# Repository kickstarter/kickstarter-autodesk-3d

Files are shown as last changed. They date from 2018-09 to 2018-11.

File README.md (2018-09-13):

# Using the Autodesk x Kickstarter FDM 3D Printer Assessment
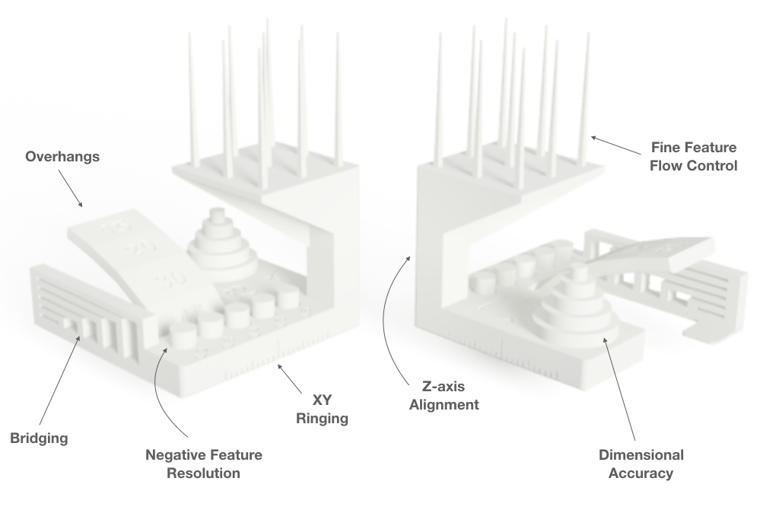
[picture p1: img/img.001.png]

## Background and Rationale
Autodesk and Kickstarter have developed a common standard that enables people to assess the performance of FDM 3D printers. (You can read more about why we undertook this initiative [here](https://www.kickstarter.com/blog/2221).) The features composing this geometry are largely based off the collaboration between Andreas Bastian and Make Magazine to develop Make Magazine’s early 3D printer shootout benchmarking protocol.

The geometry we’ve developed tests how well a printer’s hardware and software are calibrated to a given material by stressing the system to the point of failure.  The failures lead to the creation of witness features that can be used to assess the performance of the slicer, the extruder, and the motion system.  While this geometry and protocol can reveal many different types of problems in a system, fixing the exposed problems is out of scope for this basic assessment protocol.

It’s important to create dedicated test features and to calibrate those features to guarantee at least partial process failure: causing failure allows you to confirm that you’ve actually reached the limits of a process, and provides something discrete to measure and compare as relevant variables are changed.

Having discrete tests that each are calibrated to cause process failure, however, can become difficult to manage as the number of specialized tests grows, so having a consolidated geometry makes the process of testing a new 3D printer more manageable. We designed geometry to group non-interfering test features in the lower half of the print and places the riskier feature at the top of the print so that it doesn’t interfere with earlier test features.

## Contributing
We’re releasing with version 4 of this geometry and would like to work with the community of testers and creators to continue to refine and build upon both this test geometry and the test protocol, both for FDM and soon for SLA, SLS, and metal AM machines as well.  Please share comments, suggestions for improvements, and other ideas by opening an issue on this repo or submitting a pull request. And, be sure to tag photos of your prints with #FDMtest!

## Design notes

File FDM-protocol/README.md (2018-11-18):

## FDM Assessment Protocol

Download the [latest test geometry](./ksr_fdmtest_v4.stl) (units are mm) from the FDM-protocol folder and print the geometry using ESUN PLA+ Cool White filament, available in both [1.75mm](https://www.amazon.com/gp/product/B01EKEMFQS) and [2.85mm](https://www.amazon.com/dp/B01EKFV60S/) sizes using “standard” settings (i.e. all default settings).  It is very important to use the same material, as rheological and thermal properties of materials can vary dramatically between manufacturers, effectively invalidating any results obtained without controlling material properties.

What this geometry does test:

* Dimensional accuracy (backlash optional)
* Negative feature resolution
* Positive feature resolution/fine flow control
* Basic overhang capabilities
* Basic bridging capabilities
* XY ringing
* Z-axis alignment

What this geometry does not test:

* Warp/adhesion
* Overhang capabilities over a range of features (concave, convex, etc)
* Slicer handling of fine XY plane features (positive and negative space)
* Complex bridging situations
* Surface finish over a range of features
* Extrusion temperature optimization
* Support structure/geometry interaction

This geometry can be used both to characterize and compare different 3D printers and to tune parameters relevant to different features present in the geometry.

### 1. Dimensional Accuracy

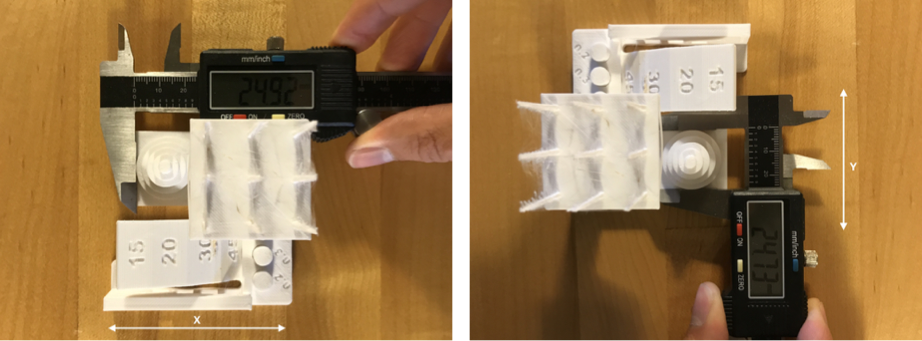
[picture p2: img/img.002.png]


*To assess dimensional accuracy, measure each tier of the dimensional accuracy stack and record the absolute different between the target and the measured dimensions in a table like so:*

**Target**|**Measured X**|**Measured Y**|**X Error**|**Y Error**
:-----:|:-----:|:-----:|:-----:|:-----:
25|24.82|24.69|0.18|0.31
20|19.93|19.75|0.07|0.25
15|14.99|14.82|0.01|0.18
10|10.01|9.85|0.01|0.15
5|4.84|4.84|0.16|0.16
Avg Err:|0.082|0.21| |
 **Average of avg. X and avg. Y error** | **0.146** | | |
Difference between avg. X and avg. Y error|0.128| | |

* Record a “1” if the magnitude of the overall average error is greater than 0.40mm.
* Record a “2” if the magnitude of the overall average error is between 0.31 and 0.40mm.
* Record a “3” if the magnitude of the overall average error is between 0.21 and 0.30mm.
* Record a “4” if the magnitude of the overall average error is 0.11 and 0.20mm.
* Record a “5” if the magnitude of the overall average error is between 0.0 and 0.10mm.

While it is not explicitly scored in this evaluation, this test also reveals the presence of backlash (or incorrectly calibrated motion systems) when the average X and average Y errors are compared.  A significant difference between the two values indicates a problem.  

### 2. Fine Flow Control

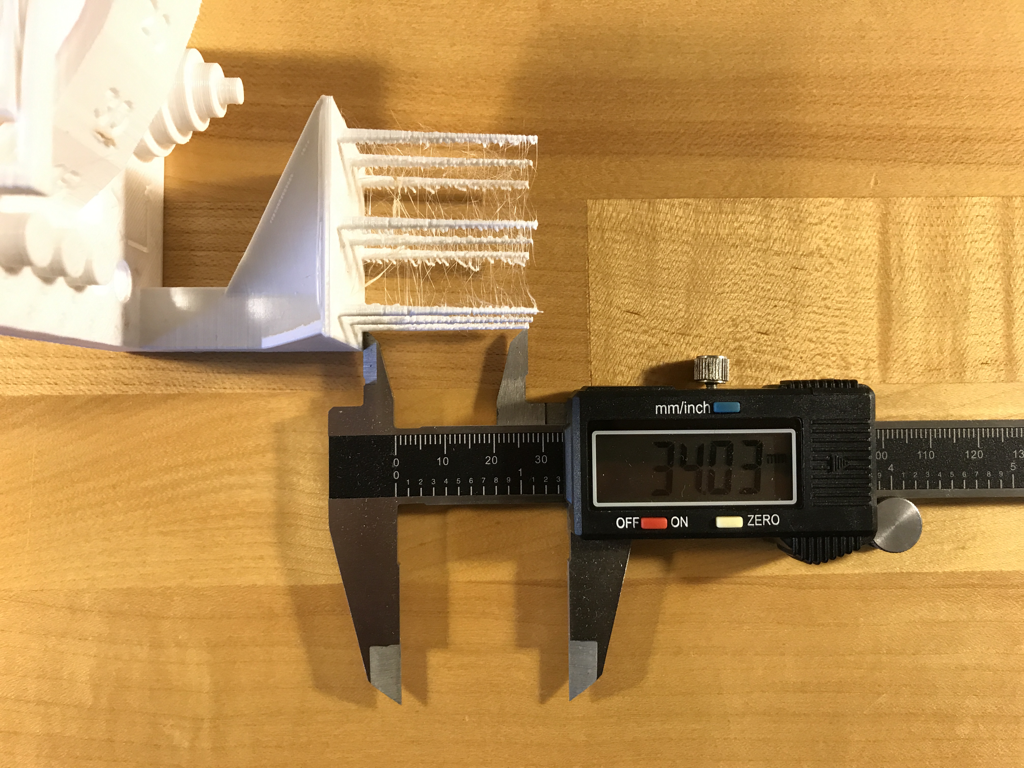
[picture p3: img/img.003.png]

*Using a pair of calipers, measure the height of the shortest spire on the top of the test print.  Visually inspect for threads of material connecting the spires.*

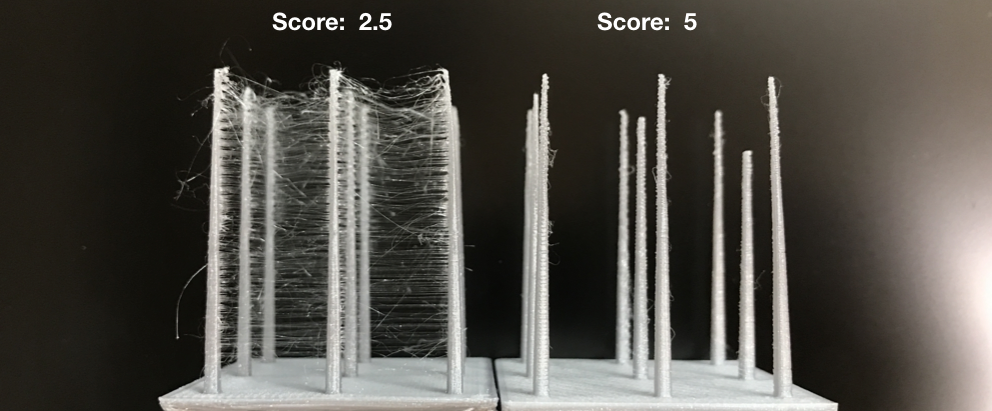
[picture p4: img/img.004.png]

*Measure the shortest spire.  This print would score 2.5.*

* If the spires are less than 30mm long, assign a 0.
* If the spires are greater than 30mm, but there is stringing between them, assign a 2.5.
* If the spires are greater than 30mm long and there is no stringing between them, assign a 5.  

### 3. Fine Negative Features

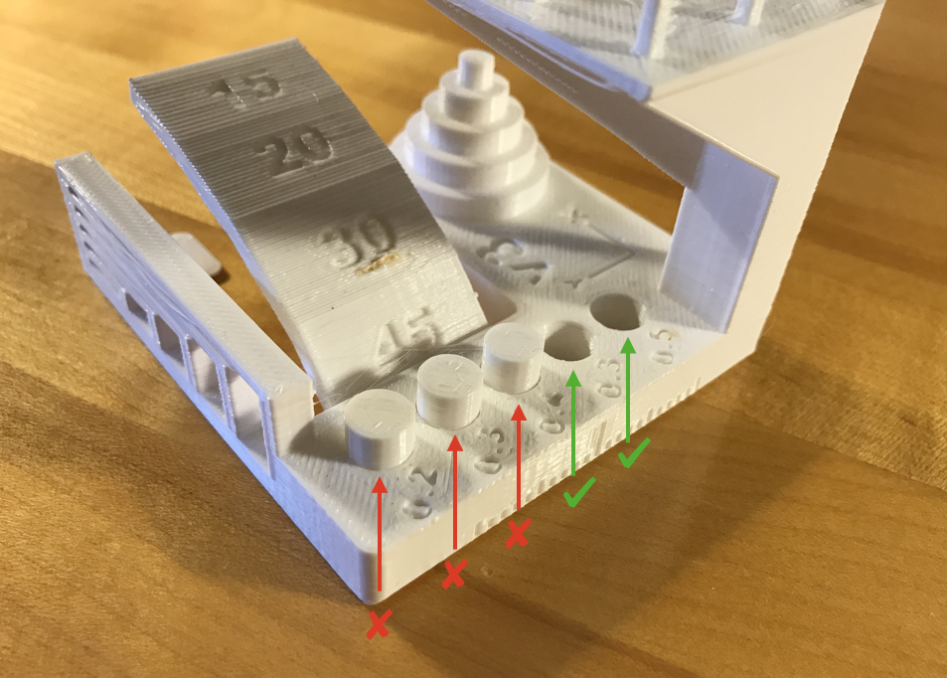
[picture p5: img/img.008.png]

*Attempt to remove all the pins from their holes using fingers (no tools).  The example above would score 2.*

* Record a “0” if no pins can be removed.
* Record a “1” if 1 pin can be removed.
* Record a “2” if 2 pins can be removed.
* Record a “3” if 3 pins can be removed.
* Record a “4” if 4 pins can be removed.
* Record a “5” if all pins can be removed.

### 4. Overhangs

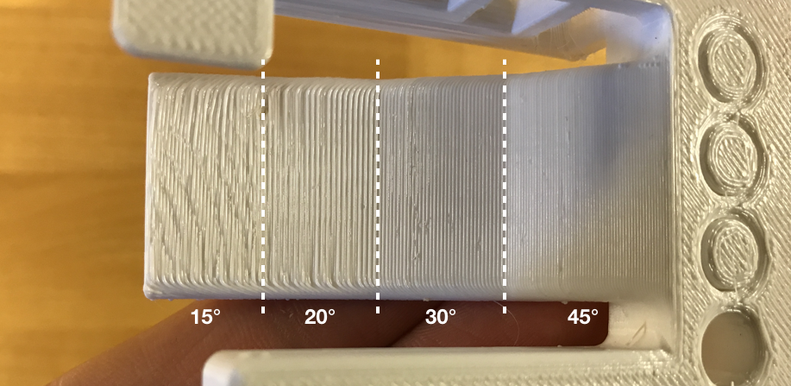
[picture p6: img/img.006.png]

*Inspect the overhang surfaces.  This print would score 3.*
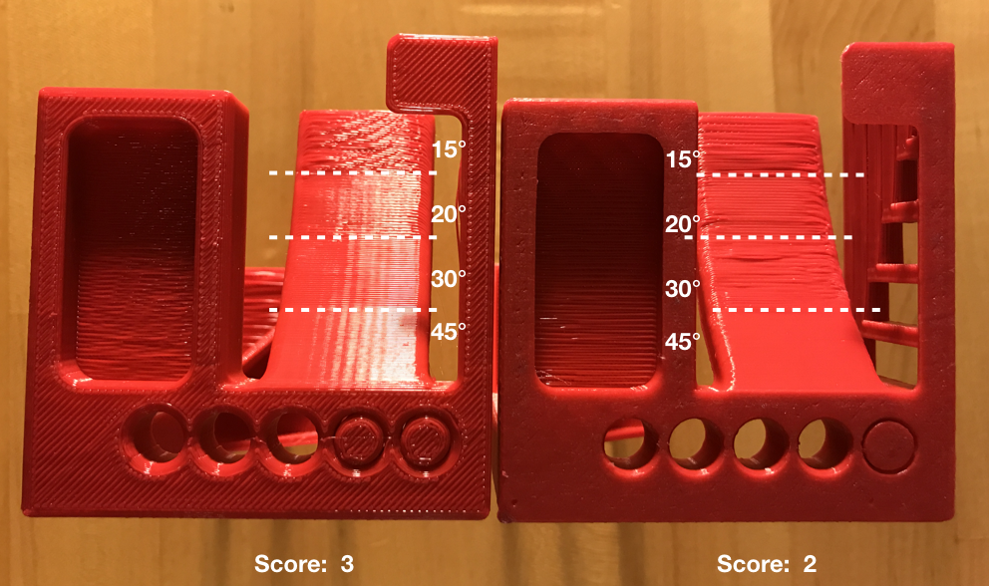
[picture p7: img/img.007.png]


* Record a “1” if the printer compiled the geometry but dropped loops and infill on the 15, 20, and 30 degree overhangs.
* Record a “3” if only the 15 and 20 degree surfaces differ from the 45 degree overhang.
* Record a “4” if only the 15 degree overhang differs from the 45 degree overhang.
* Record a “5” if there the surface finish between all four overhang surfaces is equivalent.

### 5. Bridging

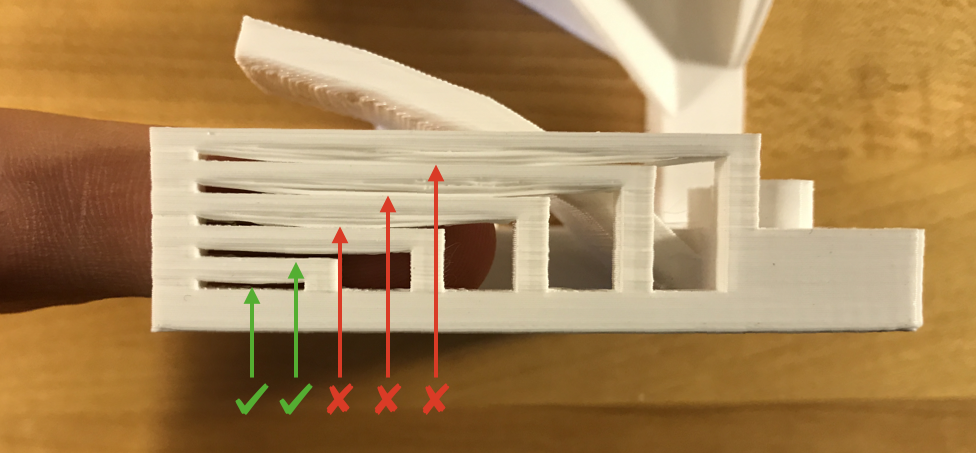
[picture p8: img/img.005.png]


Inspect for contact between bridges and the surface beneath each.  This example would score 2.  

* Record a “1” if more than 3 are in contact with the surfaces beneath them.
* Record a “2” if 3 bridges contact the surfaces beneath them.
* Record a “3” if 2 bridges contact the surfaces beneath them.
* Record a “4” if 1 bridge contacts the surface beneath it.
* Record a “5” if no bridges contact the surfaces beneath them.

### 6. XY Resonance
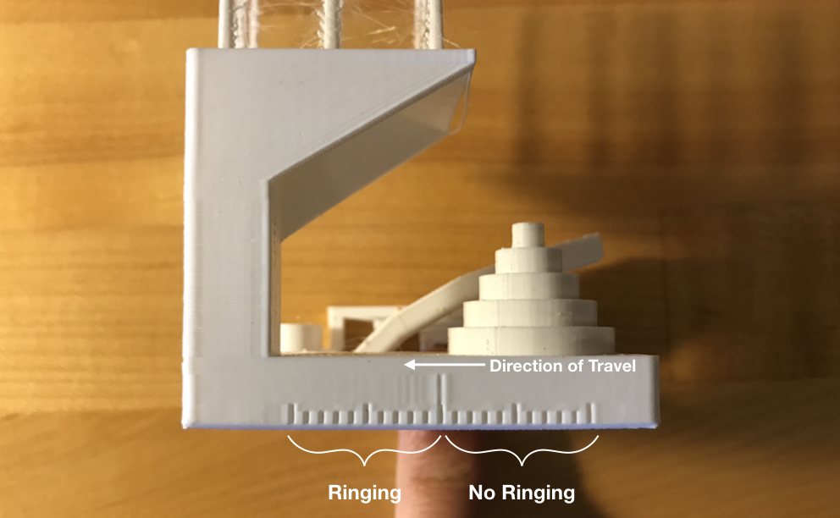
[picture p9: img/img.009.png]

*Visually inspect the X and Y ringing features, illuminating the test print from the side to highlight any ringing captured in the print.  This example would score 0.*

If rippling in the X or Y axis can be observed at or past three hash marks, record a “0”, otherwise, record a “2.5”.

### 7. Z-axis alignment

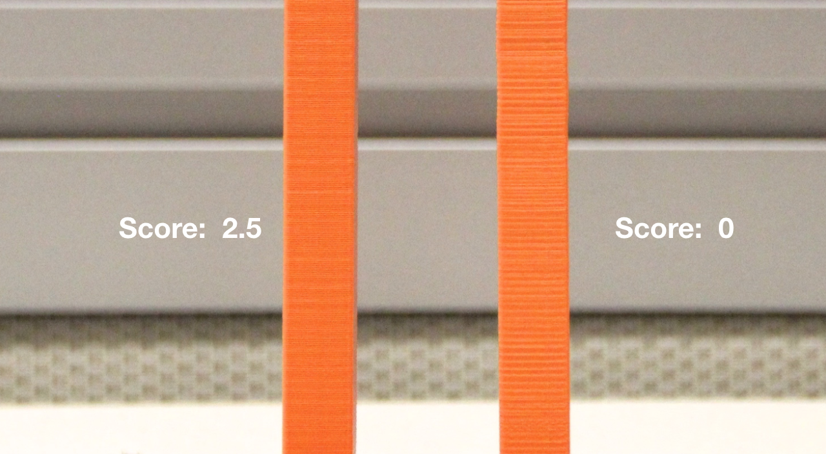
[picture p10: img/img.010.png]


If a layer registration effect with a period equal to that of the leadscrew is visible on the pillar supporting the fine positive features test, record “0,” otherwise, record “2.5.”

## Scoring
Sum the results of each section of the test protocol.  The highest possible score is 30, indicating a very well-calibrated system. For reference, a Prusa i3 MK3 scores 22.5 and a Makerbot Replicator 2 scores 18.

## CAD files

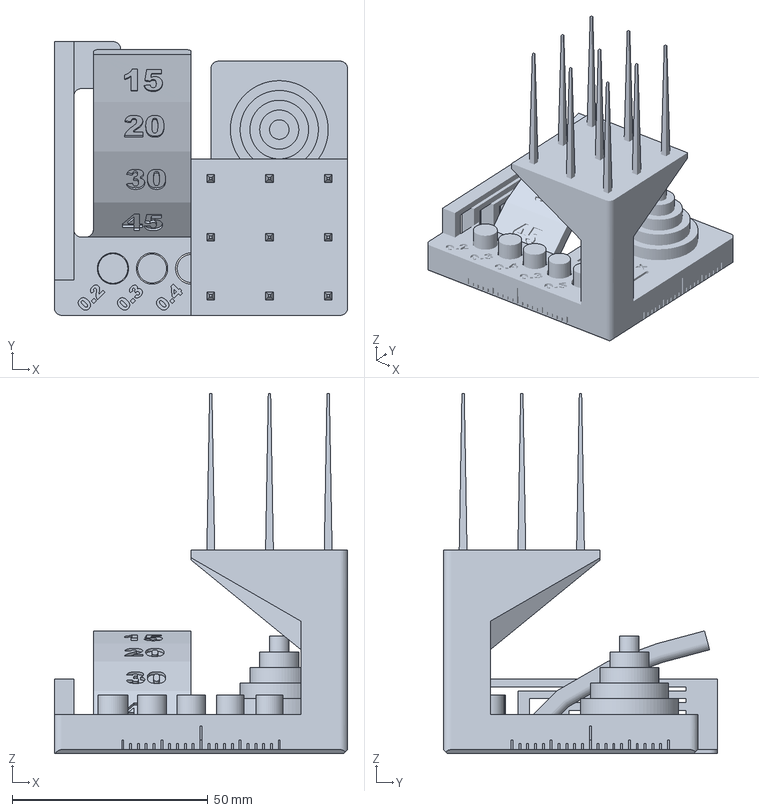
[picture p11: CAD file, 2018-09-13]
FDM-protocol/ksr_fdmtest_v4.3mf
75.0 x 70.0 x 92.0 mm

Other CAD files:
FDM-protocol/ksr_fdmtest_v4.f3d
FDM-protocol/ksr_fdmtest_v4.stl

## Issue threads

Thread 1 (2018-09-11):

Include 3MF versions?

pencerw, 2018-09-11:
3MF is lightweight, portable, and a heck of a lot better than STL ;) @andreasbastian, let me know if I can help generating the files (if you're open to including them)!

andreasbastian, 2018-09-11:
That's a great idea!  I haven't worked with 3MF much, want to maybe create a 3MF version of the geometry and then submit a pull request?  I assume 3MF is most useful when you convert from a STEP or other more data-rich format than STL, is the f3d file a reasonable place to start or should I send you a STEP/IGES?

pencerw, 2018-09-11:
@andreasbastian yeah, starting from CAD would make the most sense. Want to attach one here?

pencerw, 2018-09-12:
@andreasbastian thanks! So, a question. 3MF has a concept of "objects," described [here](https://github.com/3MFConsortium/spec_core/blob/master/3MF%20Core%20Specification.md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). Since this is a multi-body part, there are a few ways we can describe it:
* As a 6-object part, each of which contains a single-shelled mesh
* As a single object part, which contains a 6-shelled mesh

(We could also be fancy and use ["components"](https://github.com/3MFConsortium/spec_core/blob/master/3MF%20Core%20Specification.md#42-components), in which case we would have a 2-object part, one of which is a component which is repeated 5 times with transforms. This would be slick but maybe a little too clever for the intended use.)

I'm attaching screenshots from Element - see the object browser for a sense of how this works. Which do you think is more appropriate for the application? The actual 3MF files (which you can also open in Element, Meshmixer, Netfabb, etc) are attached as well.

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
[3mf options.zip](https://github.com/kickstarter/kickstarter-autodesk-3d/files/2374560/3mf.options.zip)

andreasbastian, 2018-09-13:
Nice, I think that the single object 3mf version will be best here to ensure that the cylindrical pins always stay in the exact same positions relative to the main body.  Had I modeled this so that the holes that the pins reside in change diameter, using the component trick would have been slick, but I change the pin diameters, so each has to stay in its respective hole.

Is there anything else that you'd like to change in the "one object.3mf" file or should I rename it "ksr_fdmtest_v4.3mf" and add it to the FDM protocol folder?  Thanks again for making the file!

pencerw, 2018-09-13:
Ah ah! Sorry I didn't notice the differing sizes.

I'll make the PR in just a minute!

Closed 2018-09-13.

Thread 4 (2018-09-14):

How about to make a centre rod 5mm higher ?

fred2088, 2018-09-14:
in order to test how it spread the heat away when in a small spot print area for each layer ?

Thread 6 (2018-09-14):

Bad method of calculating dimensional accuracy

drzejkopf, 2018-09-14:
In presented example, X error and Y error values are presented as positive or negative values, while they should be presented as absolute values. For example, let's assume we've got following X measurements: 26mm, 19mm, 15mm, 9.5mm, 4.5mm, then, using current method X Error (X Error=Measuerd X - Target) will be: 1mm, -1mm, 0mm, -0.5mm, 0.5mm, and then average error will be 0, while real error is huge. Method should be changed to use absolute values as X Error and Y Error values (X,Y Error=abs(Measured X,Y - Target)

andreasbastian, 2018-10-01:
Great catch, this is definitely incorrect!  Just pushed an update to the FDM protocol fixing this.

Closed 2018-10-01.

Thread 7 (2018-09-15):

Additional specifications

schbrownie, 2018-09-15:
Specifically regarding the FFF (FDM) comparison, if the goal is to get an apples-to-apples comparison between printers, then we should also specify the nozzle diameter and layer height to be used.

andreasbastian, 2018-11-06:
See my comment on Issue #10 for a bit of background, but the goal here is to just get a comparison of the complete system (hardware + software + electronics) while holding material constant.  By changing which variables you are holding constant and which you are observing, you can learn a lot with these types of geometries, but again, the scope here is at the "product level" rather than the subsystem level of extruders, stepper drivers, and other process parameters.

Closed 2018-11-06.

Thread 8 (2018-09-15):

Print Time

schbrownie, 2018-09-15:
If we are looking to get a true apples-to-apples comparison between printers, the amount of time spent printing the objects should also be taken into comparison.

Just my two cents, but I would suggest that additional points be allocated towards print speed with a faster time to completion being awarded more points than slower printing.  (and this should be the actual print time - not the theoretical time calculated by the slicer)

andreasbastian, 2018-11-06:
When we did the 2015 Make Magazine 3D printer shootout, we did measure print time, and I do think it is one of the areas where we see the biggest spread in performance.  Let's leave this thread open for a while to see if other people are interested in adding this to the protocol, I think it's very much worth exploring.

The main reason that I didn't include it is that I haven't found a reliable and consistent way to measure print time across a wide variety of machines unless you are physically using a stopwatch and observing the duration of the print.  Have you found any reliable and easy-to-implement methods of timing prints without manual involvement?

mlune, 2018-11-07:
I agree somewhat.
Print time as reported by the printer (no need to stand around with a stopwatch, a lot of printer firmware already supply this information) should be added to the report. But i don't think we need to add a scoring system yet. We'll need at least a hundred reports for us to be able to figure out a scale.

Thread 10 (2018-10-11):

What are the "Standart" settings?

X3msnake, 2018-10-11:
You should disclaim, or better have a config json of this so called standart!

andreasbastian, 2018-11-06:
Great question!  Standard settings are the settings that a printer/slicer/materials manufacturer/provider prescribe for using their product.  I find this is a good way to evaluate how well "tuned" a shipping system (hardware, software, plus materials) actually is.   That being said, individual parts of a system can be further probed by deviating from "standard" or default settings and a subset of parameters from another system.

For the scope of this project, I'm sticking to default settings, though I'd encourage you to check out the [2015 Make Magazine 3D printer Shootout models](https://www.thingiverse.com/thing:533472), which are great for doing more specific comparisons between machines/materials/slicers/electronics and associated parameters.

Closed 2018-11-06.

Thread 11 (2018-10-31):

I made a costumizable tower process to assess the correct temperature

X3msnake, 2018-10-31:
The tower OpenScad configurator code was based on Temp Calibration Tower by eibwen

The process was defined by miself, it is released under MIT feel free to reference it modify or add to the protocol if you like.

https://www.thingiverse.com/thing:3183883

andreasbastian, 2018-11-06:
This is awesome!  I think I'll:
1) start capturing some of these conversations in the Issues in the wiki and
2) start a wiki sections called "Further Testing" to collect models/protocols like this

I'd be curious to see your temperature-modification technique applied to a test geometry composed of bridging, overhang, and fine positive features:
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

andreasbastian, 2018-11-06:
Added your test to the "Further Testing" wiki page:
https://github.com/kickstarter/kickstarter-autodesk-3d/wiki/Further-Testing

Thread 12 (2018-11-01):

forgot to credit the original design

buzztiaan, 2018-11-01:
original is here ; https://www.thingiverse.com/thing:2656594

fun that you pretend 'autodesk' now made this

X3msnake, 2018-11-02:
how is this link the same work as they show here?

you have the source fusion file in the project folder but the link you provide wile not being the same it does not provide any step file only a stl the bitmaps of the 3d world

in what do you base that this project is reusing the link you shared?

buzztiaan, 2018-11-02:
idea, presentation

i do like the scoring system, but its clearly a derivative work

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

X3msnake, 2018-11-02:
Not clearly.

It is a mishmash of many ideas actually.

For example there is no stringuing test on this so called original idea and
no bridge or even the stringging test.

If that was the case then we could argue that the original before the one
you say is this

https://www.thingiverse.com/thing:182810

since this is from 2013 and the user you mention does not mention this work
anywhere...

buZz <notifications@github.com> escreveu no dia sexta, 2/11/2018 à(s) 11:14:

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

--
Com os melhores cumprimentos,
Vinicius Silva

X3msnake, 2018-11-02:
@buzztiaan

Here's some more designs the user in the design link you provided should be quoting and he is not

Make 2012
https://www.thingiverse.com/thing:33902

Make 2015
https://www.thingiverse.com/thing:533472

CTRL V 2015
https://www.thingiverse.com/thing:704409

And i'm preatty sure these go back further to the start of the reprap movement.
Guess you need to remind all these guys that they are missing out on propper creditting :)

X3msnake, 2018-11-02:
Actually here you go this is who must be quoted really:

https://www.andreasbastian.com/Andreas

Andreas Bastian is an engineer and designer interested in the blurring line between materiality, manufacturing, and design by developing new tools and frameworks.  Currently a principal research scientist in Autodesk's Office fo the CTO (OCTO), he studies generative design technologies and their applications.

Make 2015
https://www.thingiverse.com/thing:533472

Oh! wait... this is the same guy that is responsible for this project... guess he failed to give credit to himself... oops!

:D

buzztiaan, 2018-11-02:
well its good to see you already pick up source references :) thanks

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

X3msnake, 2018-11-02:
@buzztiaan the most important thing to keep out of this is that @andreasbastian is in fact the source of these designs, not majda107 like you claimed :)

buzztiaan, 2018-11-02:
as long as the history gets added, i dont care who is included in it :)

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

andreasbastian, 2018-11-06:
Hi @buzztiaan,

@X3msnake is correct, I designed the predecessors to this model with Make Magazine in 2014/15.  See more about my rationale for separate models in [this blog post](https://makezine.com/2014/11/07/what-is-print-quality/) and a breakdown of the feature-based scoring of individual models [here](https://makezine.com/2014/11/07/how-to-evaluate-the-2015-make-3dp-test-probes/
).

buzztiaan, 2018-11-06:
so it belongs to makezine as you published it through them, not autodesk

On Tue, Nov 6, 2018 at 8:04 AM Andreas Bastian <notifications@github.com>
wrote:

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

Closed 2018-11-06.

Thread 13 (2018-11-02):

FDM Protocol Text Error

jtmack1, 2018-11-02:
Looks like a score might be missing in the FDM Protocol, under "Overhangs". 1, 3, 4, and 5 are listed, but not 2. The photo above shows a print with a score of 2.

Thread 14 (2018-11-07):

Results - Ultimaker 2+

BlackHagenDesign, 2018-11-07:
We ran the test print on an Ultimaker 2 which has been upgraded with Ultimaker 2+ parts set.

Material: PLA

Nozzle: 0.4mm

Layer Height: 0.1mm

Infill: 20%

Generate supports: No

Print time: 9h 32min

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

X3msnake, 2018-11-07:
Looks like you have to tune up the retraction params

X3msnake, 2018-11-07:
What PLA Brand did u use?

BlackHagenDesign, 2018-11-07:
Material used is:

Ultimaker-NFC-PLA/PearlWhite | 1 | PLA FILAMENT .75kg   Ultimaker PLA Filament, 2.85mm, Pearl White

BlackHagenDesign, 2018-11-07:
> Looks like you have to tune up the retraction params

That sounds super. How do you do this on an Ultimaker 2+?

X3msnake, 2018-11-07:
Not on the ultimaker, but in Cura.

I would do a run with the Tower temperature test first to see if it is not a nozzle temperature thing first

https://github.com/kickstarter/kickstarter-autodesk-3d/wiki/Further-Testing

bleidzen, 2019-03-13:
Did you not post the score?
i cant find it =)

back2basik, 2019-12-28:
> Print time: 9h 31min

;O no way for a simple test

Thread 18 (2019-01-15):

Where to collect the results?

matyasforian, 2019-01-15:
There should be a unified place where users can submit results. Something very simple as this board would do, currently its hard to hunt down the results.

tommos23, 2019-01-18:
Where are the results?

RyanFior, 2019-07-12:
Did this ever get produced?  I just purchased the ZMorph VX and will run this if no one has before.  But no need to run if someone else already has.

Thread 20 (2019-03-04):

SLA Test Form

Sassw, 2019-03-04:
The team at formlabs who created the Form2 SLA machine have a jacad generated STL to test machines:

https://pastebin.com/XsYbhss9

The resulting testform object is very good at quantifying SLA performance down to high resolution features.

From the code you should see that it generates:

- Positive features (wires, walls, etc).
- Negative features (holes, slots, etc.).
- Structural features (bridges, overhangs, etc.).
- Dimensional accuracy (small dimensions, larger dimensions).

More explicitly:

- bridges on 2 axis
- internal thread
- hole geometry
- column geometry
- unsupported walls on 2 axis
- slots on 2 axis
- overhang angles on 2 axis
- text rendering
- hex stud
- external thread
- base definition test (print directly to build surface)

Surely it is a good candidate for comparing such machines - where each must be tested individually.

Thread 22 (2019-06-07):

Horizontal hole feature

marinajsewse, 2019-06-07:
One issue we have is horizontal holes experiencing sagging during cure/cooling process.
Any chance of adding a horizontal hole feature (maybe to the pillar?)

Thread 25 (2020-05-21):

What's with the big hole below the tower of hanoi?

gitcnd, 2020-05-21:
The underside is not flat on the bed - is that supposed to be testing something, or is it just to annoy us ?  (We can't add supports because then the overhang test won't work, ...)

gitcnd, 2020-05-21:
It is "Extrude 31" (a cut) in the timeline.

davispw, 2020-06-08:
@gitcnd What's annoying about it?  It's not part of the test protocol but it does a great job of showing bottom skin quality for bridging.  No need for supports.

gitcnd, 2020-06-08:
because the entire print will fail if this "bridge for no reason" fails - remember - this is designed to be printed on machines that are not yet properly set up.

GitWyd, 2021-11-15:
@gitcnd If a printer fails on basic overhangs, I would argue this is not the right test print. The KSR benchmark is more for performance evaluation of a well working printer, rather than initial tuning of a broken or poorly calibrated machine. Maybe start with testing bridging, stringing, overhangs, and dimensional accuracy first using separate prints and get your machine dialed in, then come back to KSR and see how well the machine is doing in comparison to other machines.

gitcnd, 2021-11-15:
@GitWyd - you'd lose that argument for sure.  This is a TEST PRINT that is specifically designed to be used to help you set up a printer !!

Having bridges under the part which is designed for testing dimensional accuracy makes no sense - the tests for bridging/overhangs/etc are *different* parts of this model already.

GitWyd, 2021-11-17:
@gitcnd Is it though? From what I gather, it is "a common standard that enables people to assess the performance of FDM 3D printers." Maybe I am wrong, but there seems to be an expectation of basic functionality e.g. a performance baseline

I do agree with you though that this hollow space should be removed from the design unless it is used for scoring in the Assessment Protocol.

gitcnd, 2021-11-17:
@GitWyd yes, they clearly state that the purpose of the test ..."provides something discrete to measure and compare as relevant variables are changed." - like I said: this is specifically designed to be used to help you set up a printer - (that's what you do when setting up a printer - change the variables to get the test print to work the best).

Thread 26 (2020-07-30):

Prusa Slicer barfs on ksr_fdmtest_v4.stl

jfree-fs, 2020-07-30:
PrusaSlicer-2.2.0+linux-x64-202003211856
Loading of a model file failed.

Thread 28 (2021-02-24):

Revisit standard settings discussion: I don't know what layer height I _should_ use?

Sloloem, 2021-02-24:
Relating to issues: #7 #8 #10 #27

It's...fairly difficult to gain a baseline level of understanding of the 3D printing world, and adding information like what is being asked for in these issues to a benchmark project like this would go a long way to helping create that easily accessible reference of basic knowledge that often permeates other hobbies.

If you'll pardon me to plead my case:

Having just setup my printer, done a few of the pre-compiled models that had prebuilt gcode bundled on an SD card, I decided I wanted to try this kickstarter test shape and compare to the known score for the model printer I have so I can see how well I've set the thing up as compared to the factory-assembled version.  Unfortunately no one seems willing or able to provide the standard settings that were used to slice the model when creating that benchmark.

In a comment for closing #10, @andreasbastian wrote "Standard settings are the settings that a printer/slicer/materials manufacturer/provider prescribe for using their product." but this doesn't actually answer any of the questions being asked or help understand how to use the model.  I've consulted every manual I can find for my printer and slicer, and nowhere does anything suggest an "optimal", "default", or "standard" layer height, infill %, infill pattern, or value for any parameter that might impact the quality or time taken to print.

I use PrusaSlicer and this is further complicated by several fairly equally recommended quality profiles ranging from "Ultradetail" to "Draft".  These profiles vary estimated print times between 2 hours and 22 hours.  The layer height settings of these profiles varies between 0.05mm and 0.3mm.  Whether supports are printed is also up in the air but doesn't vary by profile.

I _think_ they should be printed without support material and that adding supports would defeat the point of the overhang and bridging tests, but no one will write anything down to confirm or deny, officially, how I'm supposed to print this model.  The only real evidence I have is the DrVax youtube videos comparing Ender 5 and Prusa MK3 where he shows removing the print from the sheet.  In his video he doesn't have any support material on these, which are implied to be fresh from the printer.

But presumably layer height resolution can also impact how a lot of model features score like fine flow control, negative space, maybe even bridging and overhangs but I'm just guessing.  So when the readme says something like "Prusa i3 MK3 scores 22.5"...what settings were used to get that score?  At very least what basic profile or layer height?  If you included how long it took to print I could at least pick the quality profile that's nearest to that length but as it stands I am completely in the dark here.

Obviously there is almost infinite tweakability in printer and slicer settings but just by picking a different built-in profile and not knowing anything I can make a Prusa take over a day to print this model, but no one will say whether that's _the right way to do it_.  And measuring print time like suggested in #8 is almost useless without this baseline assumption of the resolution the model is being printed at since even small changes to that layer height value change the print time dramatically.

tl;dr:  Please for Pete's sake, just include the most basic print parameters for most slicers in the readme, it'll help out the newbies immeasurably and really increase consistency in benchmark data.

Rayth, 2024-08-09:
> nowhere does anything suggest an "optimal", "default", or "standard" layer height, infill %, infill pattern, or value for any parameter that might impact the quality or time taken to print.

This is because you can't be given settings like this. As with resin printing, FDM printers are all different and should really be calibrated. 2 People could have the same printer, same filament, same slicer, same model and STILL have different settings. Printers need to be calibrated.

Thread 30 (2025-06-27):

Wrong diameter gap between KSR 0.5 test

JohnSmithCYM, 2025-06-27:
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

As you can see in the BambuStudio or Prusa, the diameter gap between the fifth cylinder and its hole is 0.6mm, rather than 0.5mm. Could it be a bug and will be fixed in the future?

Same issue from https://github.com/bambulab/BambuStudio/issues/7385. @Haidiye00

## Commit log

2018-09-10 updated images, dim acc table, license, added filament links
2018-09-10 added v4 models (stl and f3d)
    [ksr_fdmtest_v4.f3d, ksr_fdmtest_v4.stl]
2018-09-13 fixed link in fdm-protocol, added stl units
2018-09-13 adding 3MF version
    Adding a single-mesh 3MF file containing the test geometry.
    [ksr_fdmtest_v4.3mf]
